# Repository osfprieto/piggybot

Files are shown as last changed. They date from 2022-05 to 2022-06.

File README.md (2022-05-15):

# Piggy bot by Piggy bot Dynamics

This repo has the software and hardware files related to Piggy bot.

## Mk1

Built on 2017 for Microsoft Garage's Sumo bot tournament. Uses the Elegoo UNO R3 Project Smart Robot Car Kit V2 with UNO R3.

## Mk2

Being built on 2022 based of the Mk1 by adding updated pieces from Elegoo UNO R3 Project Smart Robot Car Kit V4 with UNO R3.

Updating the chasis and modifying the wheel layout, using two UNO R3 boards, in parallel with two set of 7.4V battery packs.

## Libraries

[Elegoo libraries](https://www.elegoo.com/pages/arduino-kits-support-files)
[Elegoo tutorial for UNO R3 Project Smart Robot Car Kit v2](https://www.elegoo.com/blogs/arduino-projects/elegoo-smart-robot-car-kit-v3-0-plus-v3-0-v2-0-tutorial) - Also available under the [resources folder](./resources/)
[Elegoo tutorial for UNO R3 Project Smart Robot Car Kit v4](http://69.195.111.207/tutorial-download/?t=RobotCarV4.0) - Also available under the [resources folder](./resources/)

## IDE

- VS Code with Microsoft Arduino extension.
- Arduino IDE.

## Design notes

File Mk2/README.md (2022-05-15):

# Mk2

This is the bot being worked on during 2022.

This has a custom made chasis to allocate enough space for:

- 1 additional board.
- 1 battery pack.
- 2 engines.
- 4 wheels.

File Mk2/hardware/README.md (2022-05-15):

# Hardware for Mk2

Designed based off of the Elegoo Smart Robot Car kit chasis

They use 3/16" acrilic and 2/16" screw holes.

## Chasis

Basic shape of the chasis

## ChasisWithRoundCorners

Basic shape with the rounded corners

## ChasisCommonHoles

ChasisWithRoundCorners with added holes common to both the top and lower plates.

## ChasisTopPlateConnections

ChassisWithRoundCorners with added holes to connect with the adjacent plates (bottom and battery tray).

## ChasisTop

ChasisTopPlateConnections with added holes for the elements held in there:

- Elegoo UNO R3 boards with other accessories.
- Central engines.

## ChasisBottomPlateConnections

ChassisWithRoundCorners with added holes to connect with the adjacent plates (top).

## ChasisBottom

ChasisBottomPlateConnections with added holes for the elements held in there:

- Lower engines.
- Engine driver module.

## BatteryTrayPlateConnections

Tray to hold the battery packs, only the plate conections to connect to the top chasis plate.

## BatteryTray

BatteryTrayPlateConnections with added holes to hold the battery packs.

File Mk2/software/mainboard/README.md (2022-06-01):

# Software for the main board

This is the board that drives the four main engines as well as the consumes data from the sensors.

## Hardware

Board: Elegoo UNO R3 from Smart Robot Kit v2 (2017)
Driver: Arduino/Genuino UNO

## Library requirements

- Infrared comms - [IRRemote](https://www.arduino.cc/reference/en/libraries/irremote/)
  - Validated with version 3.6.1 (pending to update one deprecated function usage)

## Deploying

From the Arduino IDE, deploy to the board.

## Free analog pins

A0 (using it to receive signals from the Microbit board), A1, A2, A3

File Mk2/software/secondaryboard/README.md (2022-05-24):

# Secondary board

This is the board that handles the defense mechanisms (turning wheels).

## Hardware

Elegoo UNO R3 with TB6612 & MPU6050 chips (due to chip shortage) from Smart Robot Kit (2022).

## Free analog pins

A4, A5, A6

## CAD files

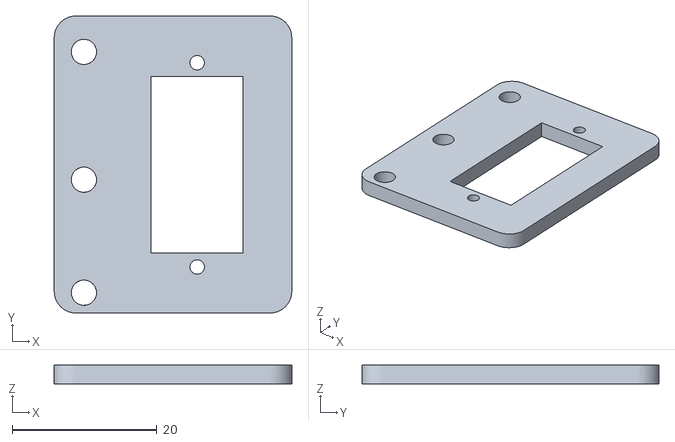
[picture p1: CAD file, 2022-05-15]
resources/ELEGOO Smart Robot Car Kit V4.0 2022.03.23/02 Manual & Main Code & APP/05 3D Model/Dead Plate.stl
32.8 x 41.0 x 2.60

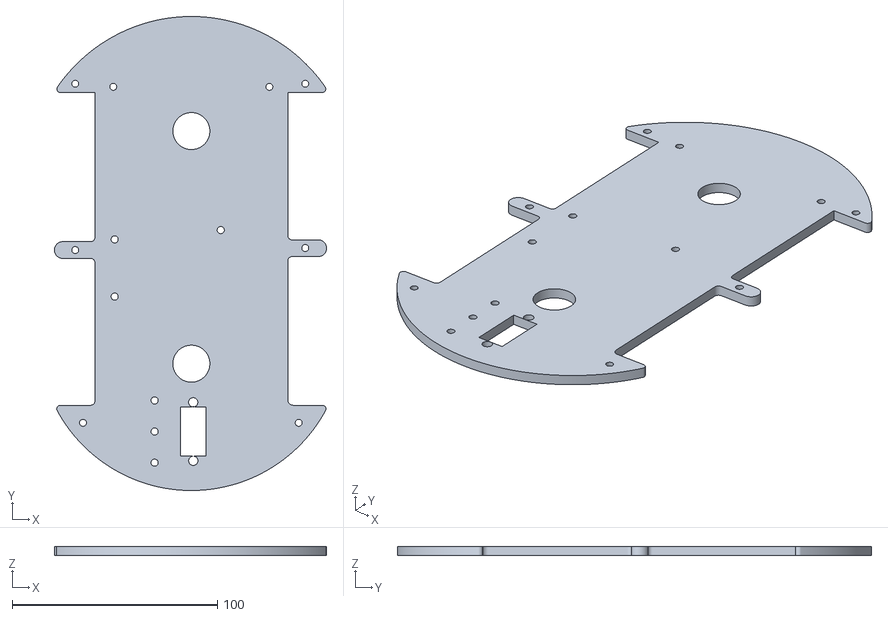
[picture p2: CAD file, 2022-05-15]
resources/ELEGOO Smart Robot Car Kit V4.0 2022.03.23/02 Manual & Main Code & APP/05 3D Model/Top Plate.stl
132.5 x 230.8 x 4.50

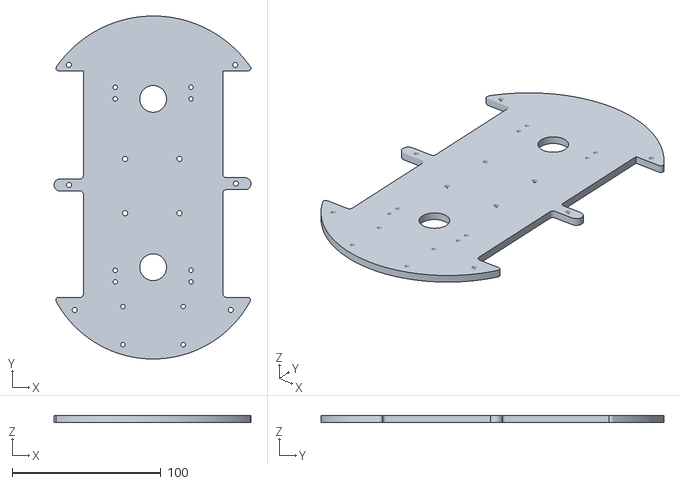
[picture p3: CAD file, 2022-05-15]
resources/ELEGOO Smart Robot Car Kit V4.0 2022.03.23/02 Manual & Main Code & APP/05 3D Model/Bottom Plate.stl
132.5 x 230.8 x 4.50

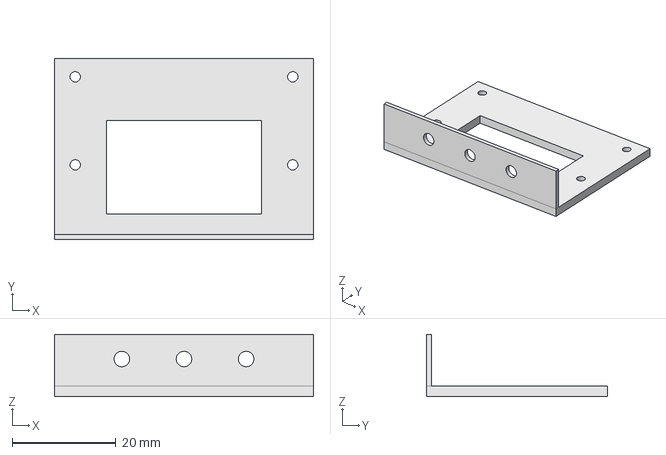
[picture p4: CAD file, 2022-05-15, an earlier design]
Mk1/hardware/sensorholder.FCStd
50.0 x 35.0 x 12.0 mm

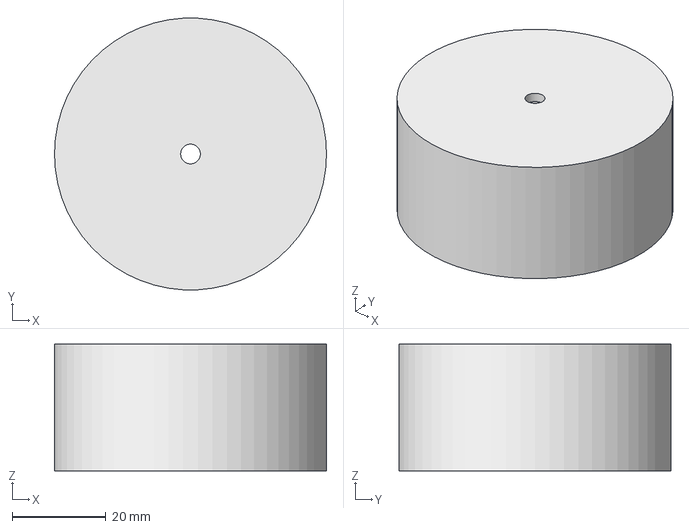
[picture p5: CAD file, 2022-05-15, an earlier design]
Mk1/hardware/Outer mold piece.FCStd
58.0 x 57.9 x 27.0 mm

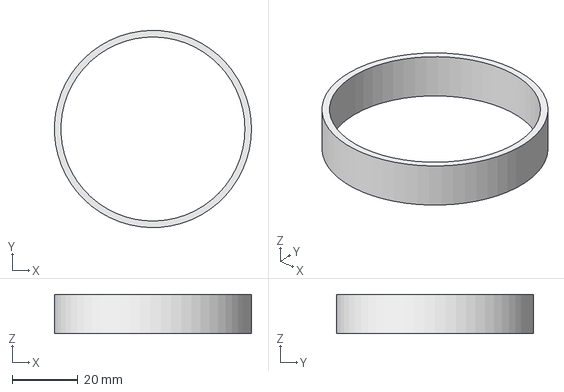
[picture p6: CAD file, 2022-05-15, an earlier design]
Mk1/hardware/Mold helper.FCStd
60.0 x 60.0 x 12.0 mm

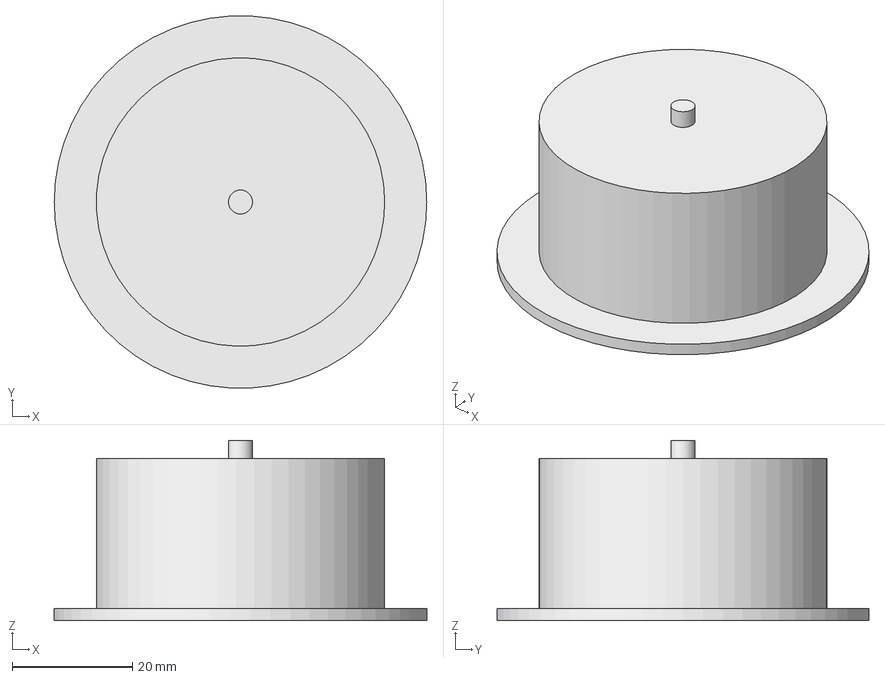
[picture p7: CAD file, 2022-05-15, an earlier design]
Mk1/hardware/Inner mold piece.FCStd
62.0 x 61.9 x 30.0 mm

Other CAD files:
Mk2/hardware/ChasisBottom.FCStd
Mk2/hardware/Brake.FCStd
Mk2/hardware/Spacer.FCStd
Mk2/hardware/ChasisTop.FCStd
Mk2/hardware/ChasisBottomPlateConnections.FCStd
Mk2/hardware/ChasisTopPlateConnections.FCStd
Mk2/hardware/BatteryTrayPlateConnection.FCStd
Mk2/hardware/BatteryTray.FCStd
Mk2/hardware/ChasisWithCommonHoles.FCStd
Mk2/hardware/ChasisWithRoundCorners.FCStd
Mk2/hardware/Chasis.FCStd
Mk1/hardware/Inner mold piece.stl
Mk1/hardware/Mold Helper.stl
Mk1/hardware/Mold pusher.FCStd
Mk1/hardware/Mold pusher.stl
Mk1/hardware/Outer mold piece.stl
Mk1/hardware/sensorholder.stl

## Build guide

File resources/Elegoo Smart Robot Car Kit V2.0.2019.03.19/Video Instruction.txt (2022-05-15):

Thanks to Engineer Boian Mitov we now have video tutorials where you will see how to assemble the car kit step by step.

To watch video tutorial pleaserefer to below links:

Elegoo Robot Car Kit V2.0 Unboxing & Assemblying Tutorial
https://www.youtube.com/watch?v=YSNd_wSzGKA&list=PLkFeYZKRTZ8YjTfnwGjGaVc7XRuWC0rwR

Unboxing Elegoo Smart Car Arduino Robot KIT Version 3.0
https://www.youtube.com/watch?v=puHBcII1Qt8&list=PLkFeYZKRTZ8ZoGLVI1El1_pJ0S1G0nnKK

Should you have any questions during usage please feel free to let us know.

service@elegoo.com

Elegoo Team

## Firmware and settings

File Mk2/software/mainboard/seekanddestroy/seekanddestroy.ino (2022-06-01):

#include <IRremote.h>

// If LT_ returns true it means it found a white stripe.
// 0 for white, 1 elsewise
// TEST THIS ON THE SCENE!!!
#define LTL digitalRead(10) // Left - Tagged with label 2 - Port 3 in  Tracking module of the custom the board
#define LTR digitalRead(2) // Right - Tagged with label 3 - Port 5 in  Tracking module of the custom the board

// For the motor driver module
#define MAX_SPEED 255

// Infrared signal codes
#define IRL 16720605 // Left
#define IRR 16761405 // Right
#define IRF 16736925 // Forward
#define IRB 16754775 // Backwards
#define IRS 16712445 // OK - Stop
#define IRH 4294967295 // Hold any button
#define IR1 16738455 // number one
#define IR2 16750695 // number two
#define IR3 16756815 // number three
#define IR4 16724175 // number four
#define IR5 16718055 // number five
#define IR6 16743045 // number six

#define RIGHT 0
#define LEFT 1

#define ATTACK_DISTANCE 50
#define CHASE_DISTANCE 5

// Ultrasonic ports
int Echo = A4;
int Trig = A5;

// Engine output
int in1 = 6;
int in2 = 7;
int in3 = 8;
int in4 = 9;
int ENA = 5;
int ENB = 11;
int ABS = 150;

int RECV_PIN = 12;
IRrecv irrecv(RECV_PIN);
decode_results results;
unsigned long IRSignal = IR1;

int distance = 0;
int turnDirection = RIGHT;
bool movingForward = false;

// Manual override through A0 port.
int readSignal = 0;
bool charging = false;

/**
@speedLeft, @speedRight: [-255,255]
value < 0: speed backwards
value = 0: not moving
value > 0: speed forward
*/
void _mMove(int speedLeft, int speedRight)
{
  int in1Value = speedRight > 0 ? speedRight : 0;
  int in2Value = speedRight < 0 ? -speedRight : 0;
  int in3Value = speedLeft < 0 ? -speedLeft : 0;
  int in4Value = speedLeft > 0 ? speedLeft : 0;

  digitalWrite(ENA,HIGH);
  digitalWrite(ENB,HIGH);
  analogWrite(in1,in1Value);
  analogWrite(in2,in2Value);
  analogWrite(in3,in3Value);
  analogWrite(in4,in4Value);
}

/**
 * Calculates the left and right speeds (in the same direction) so the car describes a curve with a given radius parameter
 * vel: upper bound of the speeds.
 * dir: 0 ir 1, defines right or left respectively
 * radius: parameter to control how diverse are the lateral speeds
 * reverse: true means the speeds will be given in negative form (going backwards).
 */
void _mCurve(int vel, int dir, int radius, bool reverse)
{
  // VEL - VEL/(1 + RADIUS/VEL)
  // R=50 -> 34 pulgadas diametro
  // R=100 -> 45 pulgadas diametro
  // R=200 -> 79 pulgadas diametro
  // R=400 -> 124 pulgadas diametro
  // R=800 -> 172 pulgadas diametro
  double slowSpeed = round(1.0 * vel - (1.0 * vel)/(1.0 + (1.0 * radius) / (1.0 * vel) )); // VEL - VEL/(1 + RADIUS/VEL)
  int speedLeft = dir == RIGHT ? vel : slowSpeed;
  int speedRight = dir == LEFT ? vel : slowSpeed;
  _mMove(reverse ? -speedLeft : speedLeft, reverse ? -speedRight : speedRight);
}


void _mStop()
{
  digitalWrite(ENA,LOW);
  digitalWrite(ENB,LOW);
}

void _mForward()
{
  _mMove(MAX_SPEED, MAX_SPEED);
}

void _mBackward()
{
  _mMove(-MAX_SPEED, -MAX_SPEED);
}

void _mRotateLeft()
{
  _mMove(-MAX_SPEED, MAX_SPEED);
}

void _mRotateRight()
{
  _mMove(MAX_SPEED, -MAX_SPEED);
}

void _mTurn()
{
  if(turnDirection==RIGHT)
  {
    _mRotateRight();
  }
  else
  {
    _mRotateLeft();
  }
}

/**
 * Tries to get out of the way so the other bot takes itself out of the ring, and performs a counterattack
 */
void _jiuJitsuReloaded(int dir)
{
  if(dir == LEFT)
  {
    _mRotateRight();
  }
  else
  {
    _mRotateLeft();
  }
  delay(200);
  _mCurve(MAX_SPEED, dir, /* radious */ 200, /* reverse */ true); // TEST THIS ON THE SCENE!!!
  delay(700);
  _mBackward();
  delay(700);  
  if(dir == LEFT)
  {
    _mRotateLeft();
  }
  else
  {
    _mRotateRight();
  }
  delay(100);
  _mForward();
  delay(500);
}

/**
 * Tries to get out of the way so the other bot takes itself out of the ring.
 */
void _jiuJitsu(int dir)
{
  if(dir == LEFT)
  {
    _mRotateRight();
  }
  else
  {
    _mRotateLeft();
  }
  delay(200);
  _mCurve(MAX_SPEED, dir, /* radious */ 200, /* reverse */ true); // TEST THIS ON THE SCENE!!!
  delay(2500);
}

void _switchDirection()
{
  if(turnDirection==RIGHT)
  {
    turnDirection=LEFT;
  }
  else
  {
    turnDirection=RIGHT;
  }
}

 /*Ultrasonic distance measurement Sub function*/
int _measureDistance() // TEST THIS ON THE SCENE!!!
{
  digitalWrite(Trig, LOW);
  delayMicroseconds(2);
  digitalWrite(Trig, HIGH);
  delayMicroseconds(20);
  digitalWrite(Trig, LOW);
  float Fdistance = pulseIn(Echo, HIGH);
  Fdistance= Fdistance/58;
  return (int)Fdistance;
}

/**
 * @deprecated
 */
void _avoidTheLineAndAttack(bool leftTrackerTouchingLine, bool rightTrackerTouchingLine){
   if (leftTrackerTouchingLine){
     _mRotateRight();
     delay(200);
     // curve backward left
     _mCurve(MAX_SPEED, LEFT, /* radious */ 5, /* reverse */ true);

   }
   else if (rightTrackerTouchingLine){
     _mRotateLeft();
     delay(200);
     // curve backward right
     _mCurve(MAX_SPEED, RIGHT, /* radious */5, /* reverse */ true);
   }
   // Test delay duration
   delay(500);
   _mStop();
}

/**
 * @deprecated
 */
void _avoidTheLine()
{
  _mBackward();
  delay(200);
  if(!LTL && LTR) // Touching the line with the left line tracke
  {
    _mRotateRight();
    while(!LTL);
    delay(200);
    _mForward();
    delay(400);
  }
  else if (LTL && !LTR) // Touching the line with the right line tracker
  {
    _mRotateLeft();
    while(!LTR);
    delay(200);
    _mForward();
    delay(400);
  }

  // Serial.println("Avoid");
}

void setup()
{
  Serial.begin(9600);
  irrecv.enableIRIn(); // Start the receiver
  pinMode(Echo, INPUT);
  pinMode(Trig, OUTPUT);
  pinMode(in1,OUTPUT);
  pinMode(in2,OUTPUT);
  pinMode(in3,OUTPUT);
  pinMode(in4,OUTPUT);
  pinMode(ENA,OUTPUT);
  pinMode(ENB,OUTPUT);
  _mStop();
  turnDirection = random(1,3);
}

void _mAttack(){
  if(!movingForward)
  {
    _switchDirection();
    _mTurn(); // When we start moving forward we come back a bit on the other direction to compensate for the momentum we had while rotating
    delay(10);
    //_mStop();
  }
  
  _mForward();
  movingForward = true;
}

void _mChaseOnly(){
  if(distance <= ATTACK_DISTANCE)
  {
    if (distance >= CHASE_DISTANCE){
      _mAttack();
    }
    else {
      _mStop();
      movingForward = false;
    }
  }
}

unsigned long trackingTimeStart = 0;
void _trackLineBackwardsAndGoToCenter(int timeToTrack, int side)
{
  trackingTimeStart = millis();

  if(side == LEFT)
  {
    _mRotateLeft();
    delay(200);
  }
  else if(side == RIGHT)
  {
    _mRotateRight();
    delay(200);
  }

  // Track the line
  while(millis() - trackingTimeStart < timeToTrack)
  {
    if(side == LEFT && !LTL)
    {
      _mRotateLeft();
      delay(50);
    }
    else if(side == RIGHT && !LTR)
    {
      _mRotateRight();
      delay(50);
    }
    _mBackward();
    delay(10);
  }
  
  // Reset the timer.
  trackingTimeStart = 0;

  // Now, let's look for the center.
  if(side == LEFT)
  {
    _mRotateRight();
  }
  else if(side == RIGHT && !LTR)
  {
    _mRotateRight();
  }
  delay(200);
  _mForward();
  delay(800);
}

void loop()
{
  // The A0 port receives 0-3.3V of energy, we expect a signal ranging from int 0 through 667.
  // 250 is a good measure for the center
  readSignal = analogRead(A0);
  if(readSignal > 99)
  {
    charging = true;
    if(readSignal > 200 && readSignal < 300)
    {
      _mStop();
    }
    else
    {
      _mMove(readSignal > 250 ? MAX_SPEED : -MAX_SPEED, readSignal > 250 ? -MAX_SPEED : MAX_SPEED);
    }
    // Serial.println("Processed signal");
  }
  else if (charging)
  {
    _mForward();
    delay(500);
    charging = false;
    // Serial.println("Charge");
  }
  else if(irrecv.decode(&results))
  {
    if(results.value != IRH)
    {
      IRSignal = results.value;
    }
    irrecv.resume();
    // Serial.println(IRSignal);
  }
  else if (IRSignal == IR1)
  {
    distance = _measureDistance();

    if(distance<=ATTACK_DISTANCE)
    {
      _mAttack();
      // Serial.println("Attacking");
    }
    else if (!LTL || !LTR)
    {
      movingForward = false;
      _trackLineBackwardsAndGoToCenter(/* timeToTrack */ 1500, !LTL ? LEFT : RIGHT);
      // Serial.println("Trackers");
    }
    else
    {
      movingForward = false;
      _mTurn();
      // Serial.println("Turn");
    }
  }
  else if(IRSignal == IRS){
    _mStop();
  }
  else if(IRSignal == IRF){
    _mForward();
  }
  else if(IRSignal == IRB){
    _mBackward();
  }
  else if(IRSignal == IRR){
    _mRotateRight();
  }
  else if(IRSignal == IRL){
    _mRotateLeft();
  }
  else if(IRSignal == IR4){
    _jiuJitsu(LEFT);
    //_jiuJitsuReloaded(LEFT);
    IRSignal = IR1;
  }
  else if(IRSignal == IR6){
    _jiuJitsu(RIGHT);
    //_jiuJitsuReloaded(RIGHT);
    IRSignal = IR1;
  }
  else
  {
    IRSignal = IR1;
  }
}

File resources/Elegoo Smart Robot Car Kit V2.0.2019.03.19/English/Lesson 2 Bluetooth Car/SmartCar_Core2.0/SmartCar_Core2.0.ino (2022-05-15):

#include <Servo.h>  



#define RECV_PIN  12
#define ECHO_PIN  A4  
#define TRIG_PIN  A5 
#define ENA 5
#define ENB 11
#define IN1 6
#define IN2 7
#define IN3 8
#define IN4 9
#define LED_Pin 13
#define LineTeacking_Pin_Right  10
#define LineTeacking_Pin_Middle 4
#define LineTeacking_Pin_Left   2
#define LineTeacking_Read_Right   !digitalRead(10)
#define LineTeacking_Read_Middle  !digitalRead(4)
#define LineTeacking_Read_Left    !digitalRead(2)
#define carSpeed 250

Servo servo;
unsigned long IR_PreMillis;
unsigned long LT_PreMillis;
int rightDistance = 0, leftDistance = 0, middleDistance = 0;

enum FUNCTIONMODE{
  IDLE,
  LineTeacking,
  ObstaclesAvoidance,
  Bluetooth,
  IRremote
} func_mode = IDLE;

enum MOTIONMODE {
  STOP,
  FORWARD,
  BACK,
  LEFT,
  RIGHT
} mov_mode = STOP;

void delays(unsigned long t) {
  for(unsigned long i = 0; i < t; i++) {
    getBTData();
    delay(1);
  }
}

int getDistance() {
  digitalWrite(TRIG_PIN, LOW);
  delayMicroseconds(2);
  digitalWrite(TRIG_PIN, HIGH);
  delayMicroseconds(10);
  digitalWrite(TRIG_PIN, LOW);
  return (int)pulseIn(ECHO_PIN, HIGH) / 58;
}

void forward(bool debug = false){ 
  analogWrite(ENA, carSpeed);
  analogWrite(ENB, carSpeed);
  digitalWrite(IN1,HIGH);
  digitalWrite(IN2,LOW);
  digitalWrite(IN3,LOW);
  digitalWrite(IN4,HIGH);
  if(debug) Serial.println("Go forward!");
}

void back(bool debug = false){
  analogWrite(ENA, carSpeed);
  analogWrite(ENB, carSpeed);
  digitalWrite(IN1,LOW);
  digitalWrite(IN2,HIGH);
  digitalWrite(IN3,HIGH);
  digitalWrite(IN4,LOW);
  if(debug) Serial.println("Go back!");
}

void left(bool debug = false){
  analogWrite(ENA,carSpeed);
  analogWrite(ENB,carSpeed);
  digitalWrite(IN1,LOW);
  digitalWrite(IN2,HIGH);
  digitalWrite(IN3,LOW);
  digitalWrite(IN4,HIGH); 
  if(debug) Serial.println("Go left!");
}

void right(bool debug = false){
  analogWrite(ENA,carSpeed);
  analogWrite(ENB,carSpeed);
  digitalWrite(IN1,HIGH);
  digitalWrite(IN2,LOW);
  digitalWrite(IN3,HIGH);
  digitalWrite(IN4,LOW);
  if(debug) Serial.println("Go right!");
}

void stop(bool debug = false){
  digitalWrite(ENA, LOW);
  digitalWrite(ENB, LOW);
  if(debug) Serial.println("Stop!");
}

void getBTData() {
  if(Serial.available()) {
    switch(Serial.read()) {
      case 'f': func_mode = Bluetooth; mov_mode = FORWARD;  break;
      case 'b': func_mode = Bluetooth; mov_mode = BACK;     break;
      case 'l': func_mode = Bluetooth; mov_mode = LEFT;     break;
      case 'r': func_mode = Bluetooth; mov_mode = RIGHT;    break;
      case 's': func_mode = Bluetooth; mov_mode = STOP;     break;
      case '1': func_mode = LineTeacking;                   break;
      case '2': func_mode = ObstaclesAvoidance;             break;
      default:  break;
    } 
  }
}

void bluetooth_mode() {
  if(func_mode == Bluetooth){
    switch(mov_mode){
      case FORWARD: forward();  break;
      case BACK:    back();     break;
      case LEFT:    left();     break;
      case RIGHT:   right();    break;
      case STOP:    stop();     break;
      default: break;
    }
  }
}

void line_teacking_mode() {
  if(func_mode == LineTeacking){
    if(LineTeacking_Read_Middle){
      forward();
      LT_PreMillis = millis();
    } else if(LineTeacking_Read_Right) { 
      right();
      while(LineTeacking_Read_Right) {
        getBTData();
      }
      LT_PreMillis = millis();
    } else if(LineTeacking_Read_Left) {
      left();
      while(LineTeacking_Read_Left) {
        getBTData();
      }
      LT_PreMillis = millis();
    } else {
      if(millis() - LT_PreMillis > 150){
        stop();
      }
    }
  }  
}

void obstacles_avoidance_mode() {
  if(func_mode == ObstaclesAvoidance){
    servo.write(90);
    delays(500);
    middleDistance = getDistance();
    if(middleDistance <= 40) {
      stop();
      delays(500);
      servo.write(10);
      delays(1000);
      rightDistance = getDistance();
      
      delays(500);
      servo.write(90);
      delays(1000);
      servo.write(170);
      delays(1000); 
      leftDistance = getDistance();
      
      delays(500);
      servo.write(90);
      delays(1000);
      if(rightDistance > leftDistance) {
        right();
        delays(360);
      } else if(rightDistance < leftDistance) {
        left();
        delays(360);
      } else if((rightDistance <= 40) || (leftDistance <= 40)) {
        back();
        delays(180);
      } else {
        forward();
      }
    } else {
        forward();
    }  
  }  
}

void setup() {
  Serial.begin(9600);
  servo.attach(3,500,2400);// 500: 0 degree  2400: 180 degree
  servo.write(90);
  pinMode(ECHO_PIN, INPUT);
  pinMode(TRIG_PIN, OUTPUT);
  pinMode(IN1, OUTPUT);
  pinMode(IN2, OUTPUT);
  pinMode(IN3, OUTPUT);
  pinMode(IN4, OUTPUT);
  pinMode(ENA, OUTPUT);
  pinMode(ENB, OUTPUT);
  pinMode(LineTeacking_Pin_Right, INPUT);
  pinMode(LineTeacking_Pin_Middle, INPUT);
  pinMode(LineTeacking_Pin_Left, INPUT);
}

void loop() {
  getBTData();
  bluetooth_mode();
  line_teacking_mode();
  obstacles_avoidance_mode();
}

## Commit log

2022-05-15 Initial commit.
    [Inner mold piece.FCStd, Inner mold piece.stl, Mold Helper.stl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]
2022-05-15 Forma inicial del chasis
    [Chasis.FCStd]
2022-05-15 ya tiene más sentido la forma, falta darle dimensiones.
    [Chasis.FCStd]
2022-05-15 Hay algo de dimensiones.
    [Chasis.FCStd]
2022-05-15 quitando lineas sobrantes
    [Chasis.FCStd]
2022-05-15 Falta definir la distancia lateral para los motores
    [Chasis.FCStd]
2022-05-15 habemus chasis
    [Chasis.FCStd]
2022-05-15 SVG del chasis basico y creacion de la siguiente etapa, chasis con huecos comunes
    [ChasisWithCommonHoles.FCStd]
2022-05-15 Updating chasis, pending to add arcs instead of diagonals
    [Chasis.FCStd, ChasisWithCommonHoles.FCStd]
2022-05-15 We now have round corners
    [ChasisWithRoundCorners.FCStd]
2022-05-15 We have common holes now.
    [ChasisWithCommonHoles.FCStd]
2022-05-15 git status
    [BatteryTray.FCStd, BatteryTrayPlateConnection.FCStd, ChasisTop.FCStd]
2022-05-15 Organizing plates, pending to finish the top and bottom plates (add the screw holes for the actual modules)
    [ChasisBottomPlateConnections.FCStd, ChasisTopPlateConnections.FCStd]
2022-05-15 Chasis bottom.
    [ChasisBottom.FCStd]
2022-05-15 Almost ready? Pending to figure out where to put the line tracker module.
    [ChasisTop.FCStd]
2022-05-16 Minor tweaks from the Surface.
    [ChasisBottom.FCStd, ChasisTop.FCStd]
2022-05-16 Line trackers proper measure.
    [ChasisBottom.FCStd]
2022-05-17 Adding engine holes to the bottom chasis.
    [ChasisBottom.FCStd]
2022-05-19 organizing line tracker modules. The one with label 1 is busted, need to find replacemoent. Moved 2 to Left.
    [seekanddestroy.ino, testLinetraker.ino]
2022-05-20 testing sensors and moving parts in main board. Pending to test infrarred as well as test moving parts in secondary board.
2022-05-20 Making sure that the movements are correct.
    [testMoving.ino]
2022-05-21 Moving seek and destroy to analog engine framework
2022-05-22 Test signal, still not working.
    [testSignal.ino]
2022-05-25 Printing to serial.
2022-05-25 Control de velocidad de llantas secundarias está configurado!!!
2022-05-25 Manual handling protocol prototype. Pending to connect the ground ports of all the boards together to clean up the noise in the signals.
    [seekanddestroy.ino, testSignalProcess.ino]
2022-05-26 Moving to analogRead since the low pass filter has been implemented in hardware.
2022-05-30 Working on the avoid and attack curves.
    [seekanddestroy.ino, testAvoidAndAttack.ino]
2022-05-30 Avoid the line and go to center.
    [seekanddestroy.ino]
